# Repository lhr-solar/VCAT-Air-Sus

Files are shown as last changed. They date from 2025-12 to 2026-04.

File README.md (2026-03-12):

# Air-Suspension Boards

> **Project:** Longhorn Racing Solar - Hardware & Telemetry
> **Author:** Karthik Kurapati 

This repository contains the hardware design files for 4 sensors on the car: Suspension (Linear Potentiometers), Pitot, Temperature/Pressure, and RideHeight. 

## Table of Contents
1. [Telemetry CAN Overview](#CAN-overview)
2. [PSOM Boards](#psom-boards)
    - [Pitot Board](#1-pitot-board)
    - [Sus-RH (Suspension & Ride Height) Board](#2-sus-rh-board)
3. [Breakout Boards](#breakout-boards)
    - [Temperature Breakout](#3-temperature-breakout)
    - [Ride Height Breakout](#4-ride-height-breakout)

---

## Telemetry CAN Overview

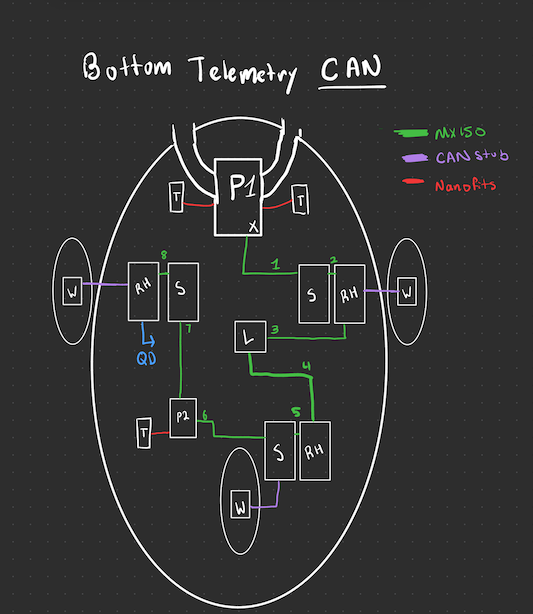
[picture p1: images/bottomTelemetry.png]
System Block Diagram


P - Pitot Board
T - Temperature Breakout
L - Telemetry Leader
S - Sus-RH Board
RH - Sus-RH Board + Ride Height Breakout
W - Wheels Board

---

## PSOM Boards

These boards integrate a PSOM to collect data from sensors 

### 1. Pitot Board
**Function:** Measures the vehicle's true airspeed via a pitot sensor. Relays data sent by the temperature sensor to telemetry leader. 
**Sensors**: HSCDRRN010NDSA3

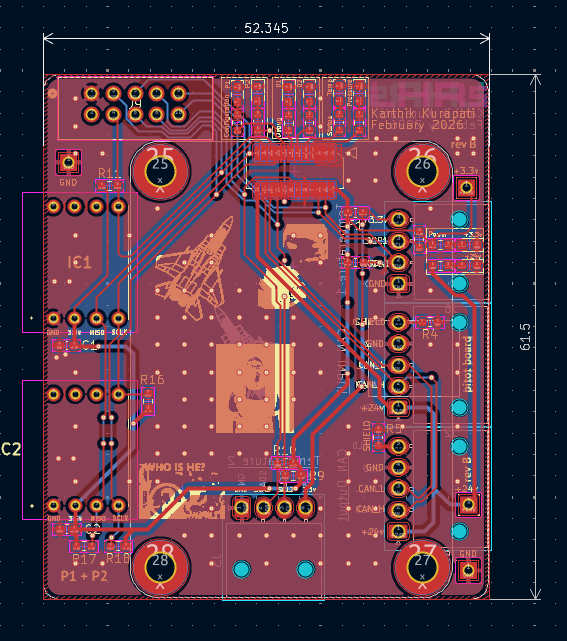
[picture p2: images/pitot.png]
Pitot Board


### 2. Sus-RH Board
**Function:** Measures linear potentiometer (suspension) travel on the car via ADC. Interfaces with ride height breakout. 
**Sensor:** LPPS-12
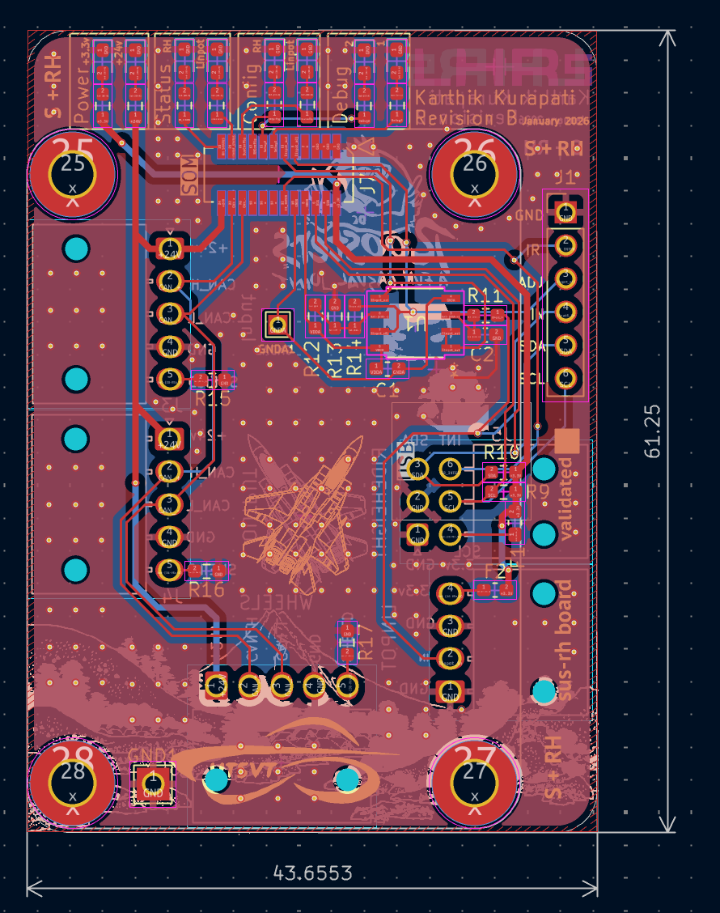
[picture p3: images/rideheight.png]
Sus-RH Board


---

## Breakout Boards

Simple boards that use nano-fits to connect to the boards above to add functionality. Both breakouts use I2C to communicate over the distance. 

### 3. Temperature Breakout
**Function:** Provide valuable temperature, pressure, humidity, and air density information to improve estimate of airspeed. 
**Sensor:** BME280 

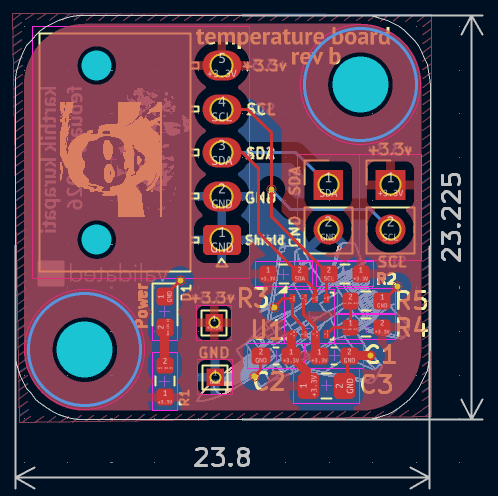
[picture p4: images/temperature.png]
Temp Breakout 3D Render/Photo


### 4. Ride Height Breakout (IR Board)
**Function:** Provides the distance from the bottom of the car to the road in multiple areas.
**Sensor** VL53L0X

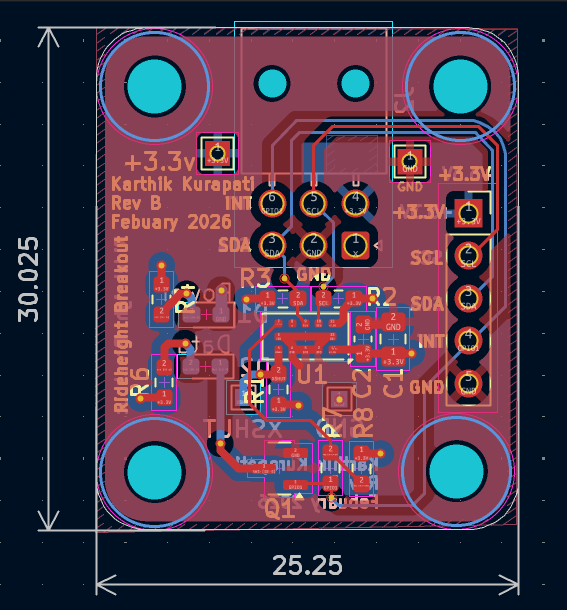
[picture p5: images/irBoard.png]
Ride Height Breakout 3D Render/Photo

---

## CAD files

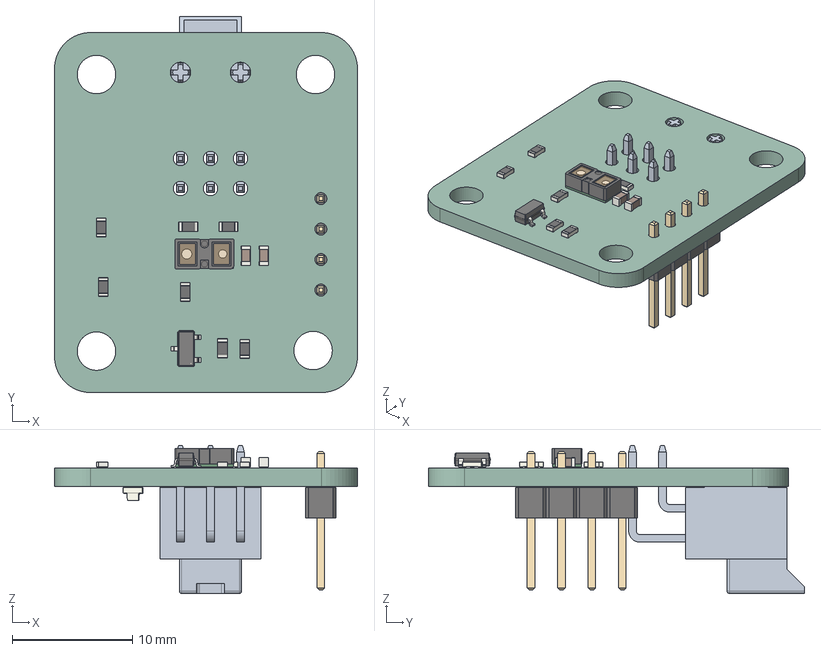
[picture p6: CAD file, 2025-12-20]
hardware/ir_board/ir_board.step
25.2 x 31.3 x 12.3 mm
ST_VL53L1x
R_0603_1608Metric x 7
C_0603_1608Metric x 2
SOT-23
LED_0603_1608Metric x 2
PinHeader_1x04_P2.54mm_Vertical
ir_board_PCB

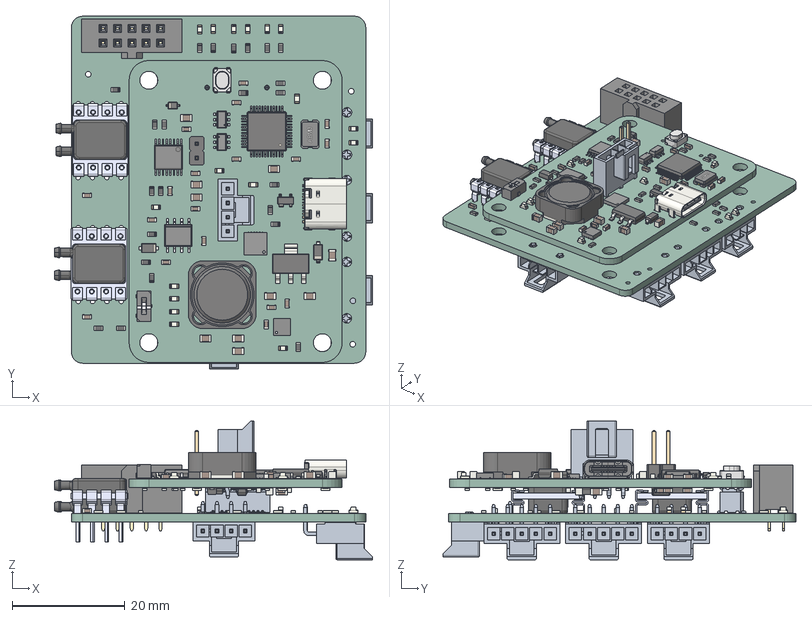
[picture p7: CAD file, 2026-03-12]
hardware/Pitot/Pitot.step
56.3 x 62.5 x 24.6 mm
R_0603_1608Metric x 49
C_0603_1608Metric x 27
D_SOD-123F x 2
LED_0603_1608Metric x 17
ThermalPin
PinsArrayLR x 3
PinsArrayTB
C_0805_2012Metric x 12
LQFP-48_7x7mm_P0.5mm
SOT-223
kicad_embedded_DC8F7DF302591227B9F71E251B6FE682
kicad_embedded_70E7614803E5E4F918B4D78DA69A18BB
L_Coilcraft_MSS1246-XXX
USB_C_Receptacle_GCT_USB4105-xx-A_16P_TopMnt_Horizontal
kicad_embedded_9406EA57197DC5EF7108E35EAA086FA7
BODY-SO x 2
LEAD-D0008A x 8
TL3365AF180QG--3DModel-STEP-520916
BODY-TSSOP
LEAD-TSSOP x 16
PIN1
DAP
SOT-143
D_SOD-123
PinHeader_1x02_P2.54mm_Vertical
D_SOD-323
SOT-23W
LEAD-SO x 8
PeripheralSOM_PCB
Fuse_0603_1608Metric
HSCDRRN010NDSA3 x 2
SFH11-xC-Dx-ST-BK body_05
pin^SFH11-xC-Dx-ST-BK Ass x 10
Pitot_PCB

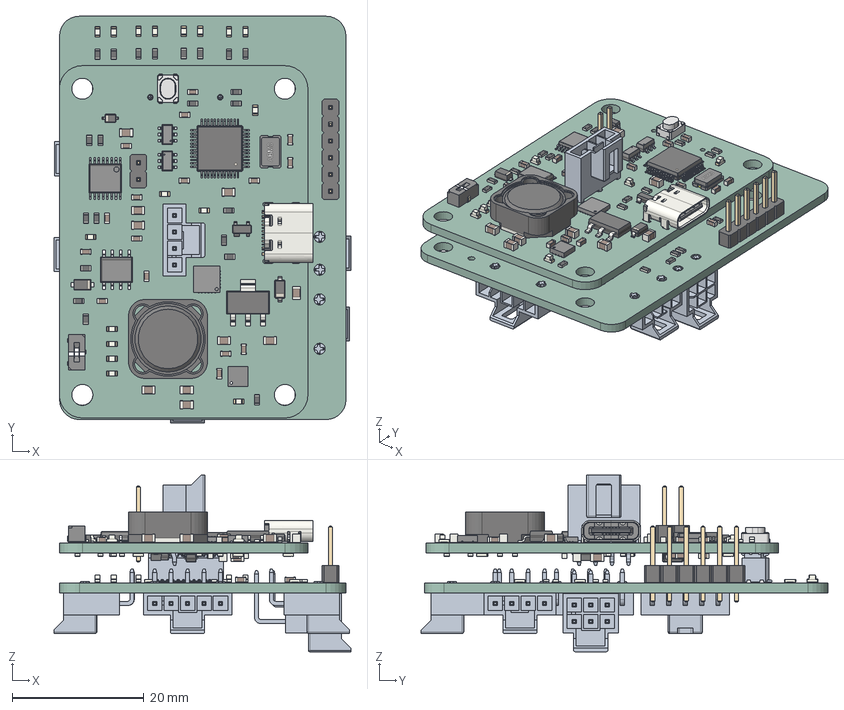
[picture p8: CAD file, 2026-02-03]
hardware/Sus-RH/Sus-RH.step
45.1 x 61.7 x 26.8 mm
LED_0603_1608Metric x 17
Fuse_0603_1608Metric x 2
R_0603_1608Metric x 48
C_0603_1608Metric x 27
D_SOD-123F x 2
ThermalPin
PinsArrayLR x 3
PinsArrayTB
C_0805_2012Metric x 12
LQFP-48_7x7mm_P0.5mm
SOT-223
kicad_embedded_DC8F7DF302591227B9F71E251B6FE682
kicad_embedded_70E7614803E5E4F918B4D78DA69A18BB
L_Coilcraft_MSS1246-XXX
USB_C_Receptacle_GCT_USB4105-xx-A_16P_TopMnt_Horizontal
kicad_embedded_9406EA57197DC5EF7108E35EAA086FA7
BODY-SO x 2
LEAD-D0008A x 8
TL3365AF180QG--3DModel-STEP-520916
BODY-TSSOP
LEAD-TSSOP x 16
PIN1
DAP
SOT-143
D_SOD-123
PinHeader_1x02_P2.54mm_Vertical
D_SOD-323
SOT-23W
LEAD-SO x 8
PeripheralSOM_PCB
PinHeader_1x06_P2.54mm_Vertical
Sus-RH_PCB

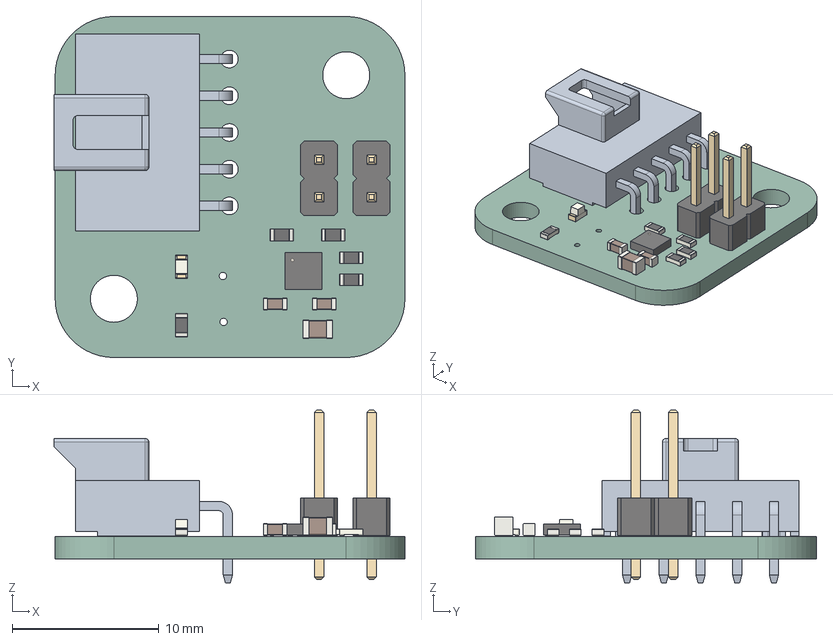
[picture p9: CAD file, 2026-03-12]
hardware/TempBoard/TempBoard.step
23.9 x 23.2 x 11.8 mm
R_0603_1608Metric x 5
C_0603_1608Metric x 2
Bosch_LGA-8_2.5x2.5mm_P0.65mm_ClockwisePinNumbering
C_0805_2012Metric
LED_0603_1608Metric
PinHeader_1x02_P2.54mm_Vertical x 2
TempBoard_PCB

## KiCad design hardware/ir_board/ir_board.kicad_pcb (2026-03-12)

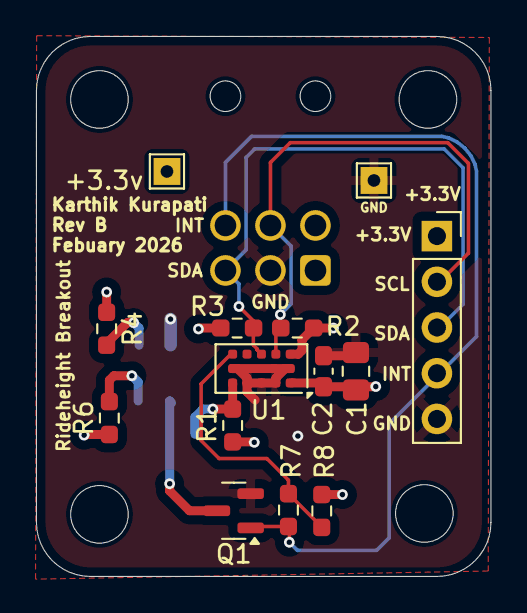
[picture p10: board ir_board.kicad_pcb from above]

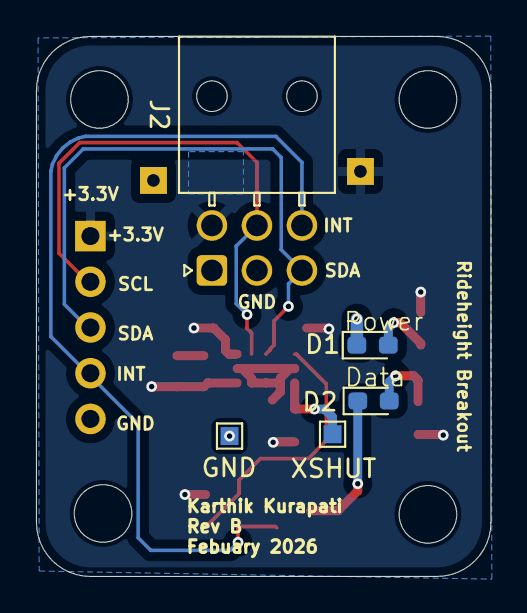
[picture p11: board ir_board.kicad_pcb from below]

Board: 2 copper layers, 25.2 x 30.0 mm, 23 parts (5 on the bottom side), 10 nets.

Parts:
+3.3v: TestPoint; TestPoint_THTPad_1.5x1.5mm_Drill0.7mm
C1: 4.7uf; C_0805_2012Metric_Pad1.18x1.45mm_HandSolder
C2: 0.1uf; C_0603_1608Metric_Pad1.08x0.95mm_HandSolder
D1, D2: LED; LED_0603_1608Metric_Pad1.05x0.95mm_HandSolder
GND: TestPoint; TestPoint_THTPad_1.5x1.5mm_Drill0.7mm
GND#2: TestPoint; TestPoint_Pad_1.0x1.0mm
H1, H2, H3, H4: MountingHole; MountingHole_3.2mm_M3
J1: Conn_01x05; PinSocket_1x05_P2.54mm_Vertical
J2: Conn_01x06; Molex_Nano-Fit_105314-xx06_2x03_P2.50mm_Horizontal
Q1: IRLML0030; SOT-23
R1: 10k; R_0603_1608Metric_Pad0.98x0.95mm_HandSolder
R2, R3, R8: 4.7k; R_0603_1608Metric_Pad0.98x0.95mm_HandSolder
R4, R6: 1k; R_0603_1608Metric_Pad0.98x0.95mm_HandSolder
R7: 0; R_0603_1608Metric_Pad0.98x0.95mm_HandSolder
U1: VL53L0CXV0DH1; ST_VL53L1x
XSHUT: TestPoint; TestPoint_Pad_1.0x1.0mm

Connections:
+3.3V: +3.3v.1, C1.1, C2.1, J1.1, J2.4, R1.1, R2.1, R3.1, R4.1, R6.1, R8.1, U1.1 (AVDDVCSEL), U1.11 (AVDD)
/GPIO1: J1.4, J2.6, Q1.1 (G), R7.1
/SCL: J1.2, J2.5, R2.2, U1.10 (SCL)
/SDA: J1.3, J2.3, R3.2, U1.9 (SDA)
/XSHUT: R1.2, U1.5 (XSHUT), XSHUT.1
GND: C1.2, C2.2, D1.1 (K), GND.1, GND#2.1, J1.5, J2.2, Q1.2 (S), U1.2 (AVSSVCSEL), U1.3 (GND), U1.4 (GND), U1.6 (GND), U1.12 (GND)
unnamed: D1.2 (A), R4.2
unnamed: D2.2 (A), R6.2
unnamed: D2.1 (K), Q1.3 (D)
unnamed: R7.2, R8.2, U1.7 (GPIO1)

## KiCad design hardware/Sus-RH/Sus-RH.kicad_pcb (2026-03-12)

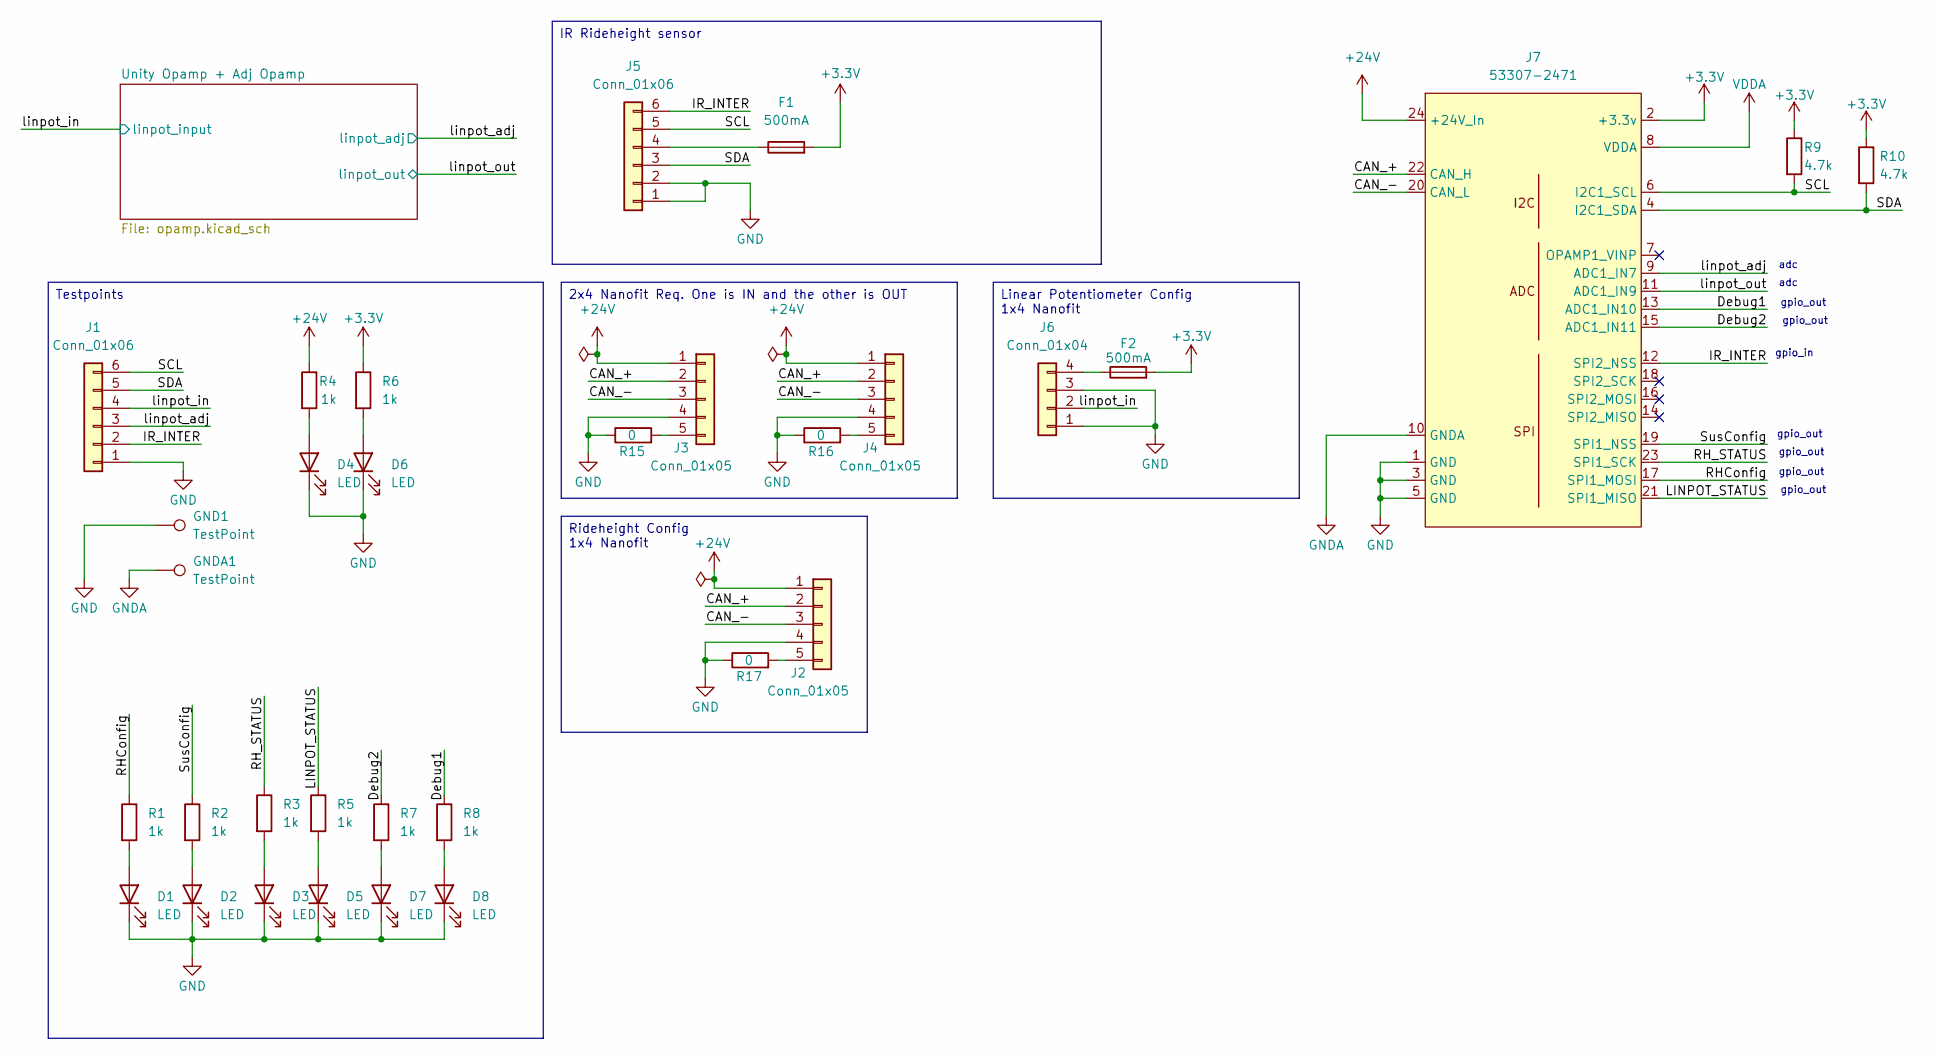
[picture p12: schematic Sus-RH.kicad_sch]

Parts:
D1, D2, D3, D4, D5, D6, D7, D8: LED; LED_0603_1608Metric_Pad1.05x0.95mm_HandSolder
F1, F2: 500mA; Fuse_0603_1608Metric_Pad1.05x0.95mm_HandSolder
GND1: TestPoint; TestPoint_THTPad_2.5x2.5mm_Drill1.2mm
GNDA1: TestPoint; TestPoint_THTPad_1.5x1.5mm_Drill0.7mm
J1: Conn_01x06; PinHeader_1x06_P2.54mm_Vertical
J2, J3, J4: Conn_01x05; Molex_Nano-Fit_105313-xx05_1x05_P2.50mm_Horizontal
J5: Conn_01x06; Molex_Nano-Fit_105314-xx06_2x03_P2.50mm_Horizontal
J6: Conn_01x04; Molex_Nano-Fit_105313-xx04_1x04_P2.50mm_Horizontal
J7: 53307-2471; PeripheralSOM
R1, R2, R3, R4, R5, R6, R7, R8: 1k; R_0603_1608Metric_Pad0.98x0.95mm_HandSolder
R9, R10: 4.7k; R_0603_1608Metric_Pad0.98x0.95mm_HandSolder
R15, R16, R17: 0; R_0603_1608Metric_Pad0.98x0.95mm_HandSolder

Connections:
+3.3V: F1.2, F2.2, J7.2 (+3.3v), R6.1, R9.1, R10.1
+24V: J2.1, J3.1, J4.1, J7.24 (+24V_In), R4.1
/CAN_+: J2.2, J3.2, J4.2, J7.22 (CAN_H)
/CAN_-: J2.3, J3.3, J4.3, J7.20 (CAN_L)
/Debug1: J7.13 (ADC1_IN10), R8.1
/Debug2: J7.15 (ADC1_IN11), R7.1
/IR_INTER: J1.2, J5.6, J7.12 (SPI2_NSS)
/LINPOT_STATUS: J7.21 (SPI1_MISO), R5.1
/RHConfig: J7.17 (SPI1_MOSI), R1.1
/RH_STATUS: J7.23 (SPI1_SCK), R3.1
/SCL: J1.6, J5.5, J7.6 (I2C1_SCL), R9.2
/SDA: J1.5, J5.3, J7.4 (I2C1_SDA), R10.2
/SusConfig: J7.19 (SPI1_NSS), R2.1
/linpot_adj: J1.3, J7.9 (ADC1_IN7); also elsewhere on the board
/linpot_in: J1.4, J6.2; also elsewhere on the board
/linpot_out: J7.11 (ADC1_IN9); also elsewhere on the board
GND: D1.1 (K), D2.1 (K), D3.1 (K), D4.1 (K), D5.1 (K), D6.1 (K), D7.1 (K), D8.1 (K), GND1.1, J1.1, J2.4, J3.4, J4.4, J5.1, J5.2, J6.1, J6.3, J7.1 (GND), J7.3 (GND), J7.5 (GND), R15.1, R16.1, R17.1; also elsewhere on the board
GNDA: GNDA1.1, J7.10 (GNDA); also elsewhere on the board
unnamed: D1.2 (A), R1.2
unnamed: D2.2 (A), R2.2
unnamed: D3.2 (A), R3.2
unnamed: D4.2 (A), R4.2
unnamed: D5.2 (A), R5.2
unnamed: D6.2 (A), R6.2
unnamed: D7.2 (A), R7.2
unnamed: D8.2 (A), R8.2
unnamed: J2.5, R17.2
unnamed: J3.5, R15.2
unnamed: J4.5, R16.2
unnamed: F1.1, J5.4
unnamed: F2.1, J6.4
VDDA: J7.8 (VDDA); also elsewhere on the board

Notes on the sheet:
gpio_in
adc
gpio_out
Rideheight Config 1x4 Nanofit
IR Rideheight sensor
2x4 Nanofit Req. One is IN and the other is OUT
Testpoints
Linear Potentiometer Config 1x4 Nanofit

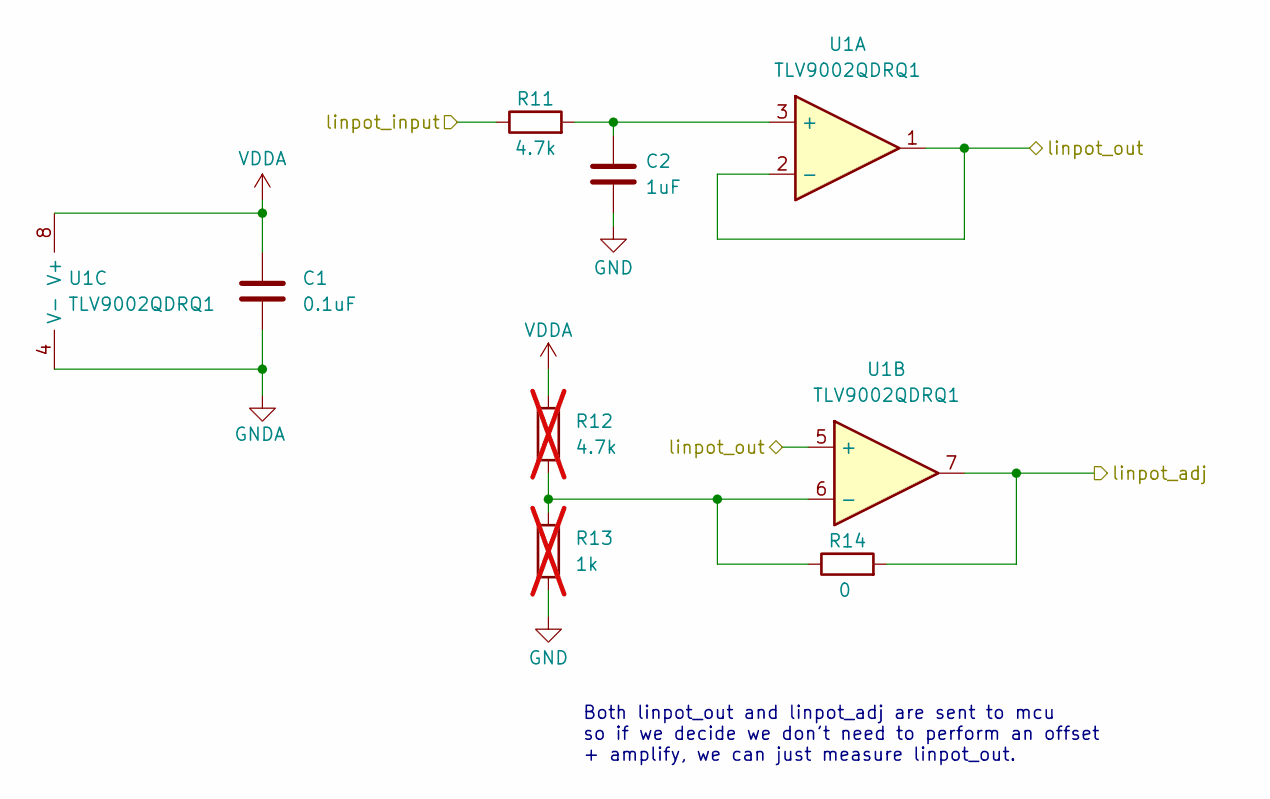
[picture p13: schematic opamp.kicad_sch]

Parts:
C1: 0.1uF; C_0603_1608Metric_Pad1.08x0.95mm_HandSolder
C2: 1uF; C_0603_1608Metric_Pad1.08x0.95mm_HandSolder
R11: 4.7k; R_0603_1608Metric_Pad0.98x0.95mm_HandSolder
R12: 4.7k; R_0603_1608Metric_Pad0.98x0.95mm_HandSolder; not fitted
R13: 1k; R_0603_1608Metric_Pad0.98x0.95mm_HandSolder; not fitted
R14: 0; R_0603_1608Metric_Pad0.98x0.95mm_HandSolder
U1: TLV9002QDRQ1; SOIC8_D_TEX; Mouser P/N 595-TLV9002QDRQ1

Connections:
/linpot_adj: R14.2, U1.7; also elsewhere on the board
/linpot_in: R11.1; also elsewhere on the board
/linpot_out: U1.1, U1.2 (-), U1.5 (+); also elsewhere on the board
GND: C2.2, R13.2; also elsewhere on the board
GNDA: C1.2, U1.4 (V-); also elsewhere on the board
unnamed: C2.1, R11.2, U1.3 (+)
unnamed: R12.2, R13.1, R14.1, U1.6 (-)
VDDA: C1.1, R12.1, U1.8 (V+); also elsewhere on the board

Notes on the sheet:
Both linpot_out and linpot_adj are sent to mcu so if we decide we don't need to perform an offset + amplify, we can just measure linpot_out.

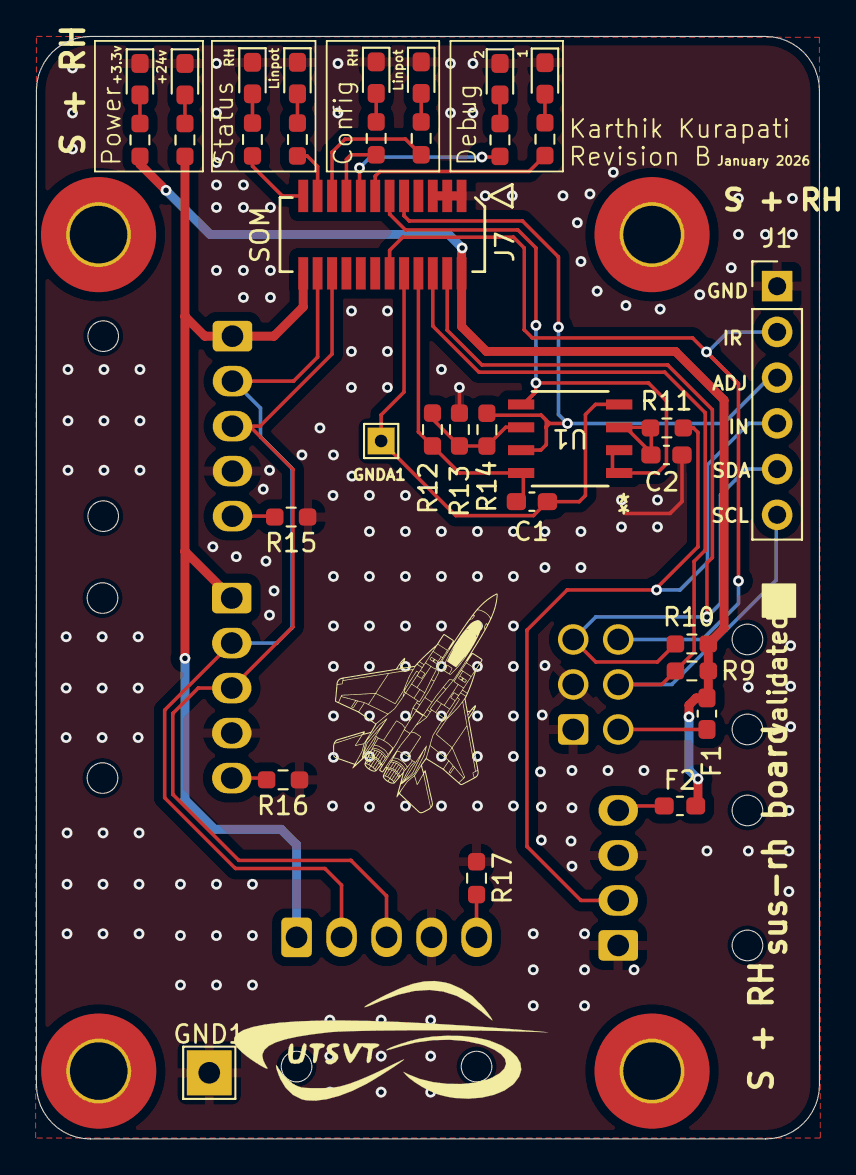
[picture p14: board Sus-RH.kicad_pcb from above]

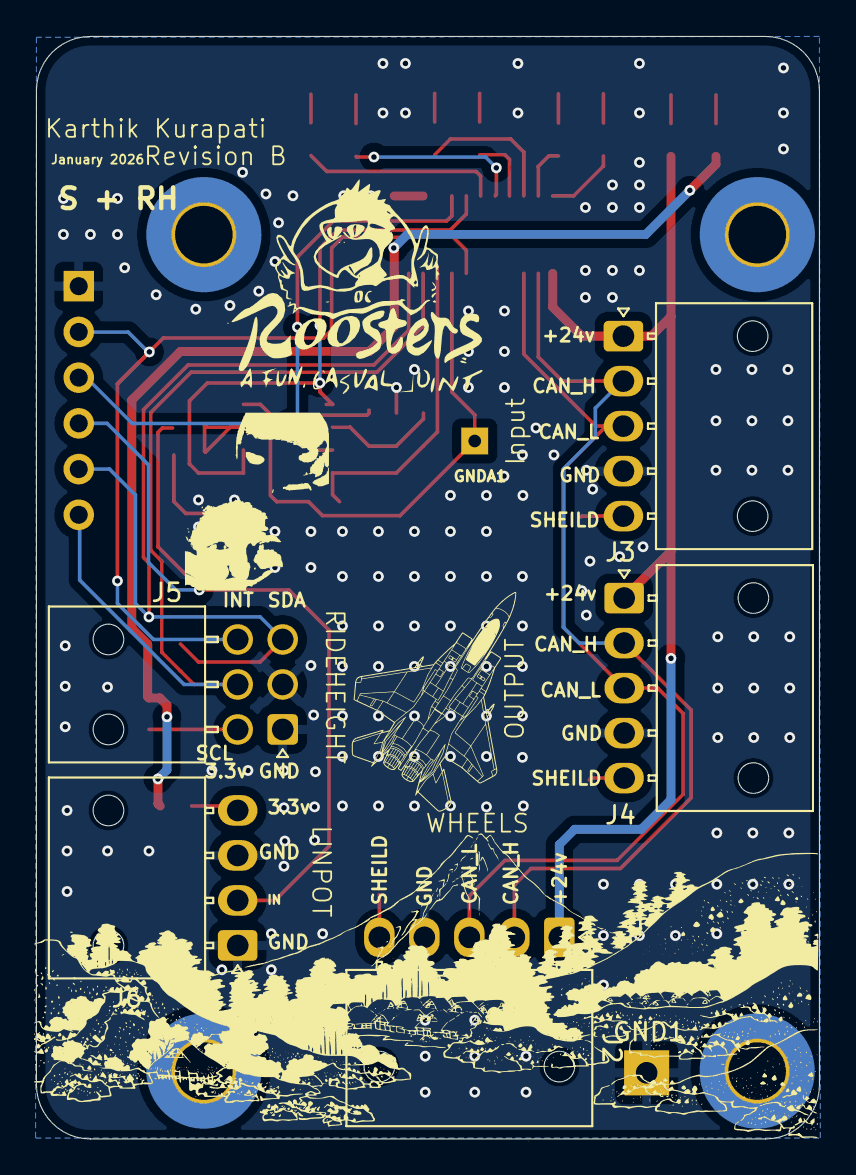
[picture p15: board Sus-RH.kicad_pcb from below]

Board: 2 copper layers, 43.5 x 61.2 mm, 39 parts (5 on the bottom side), 34 nets.

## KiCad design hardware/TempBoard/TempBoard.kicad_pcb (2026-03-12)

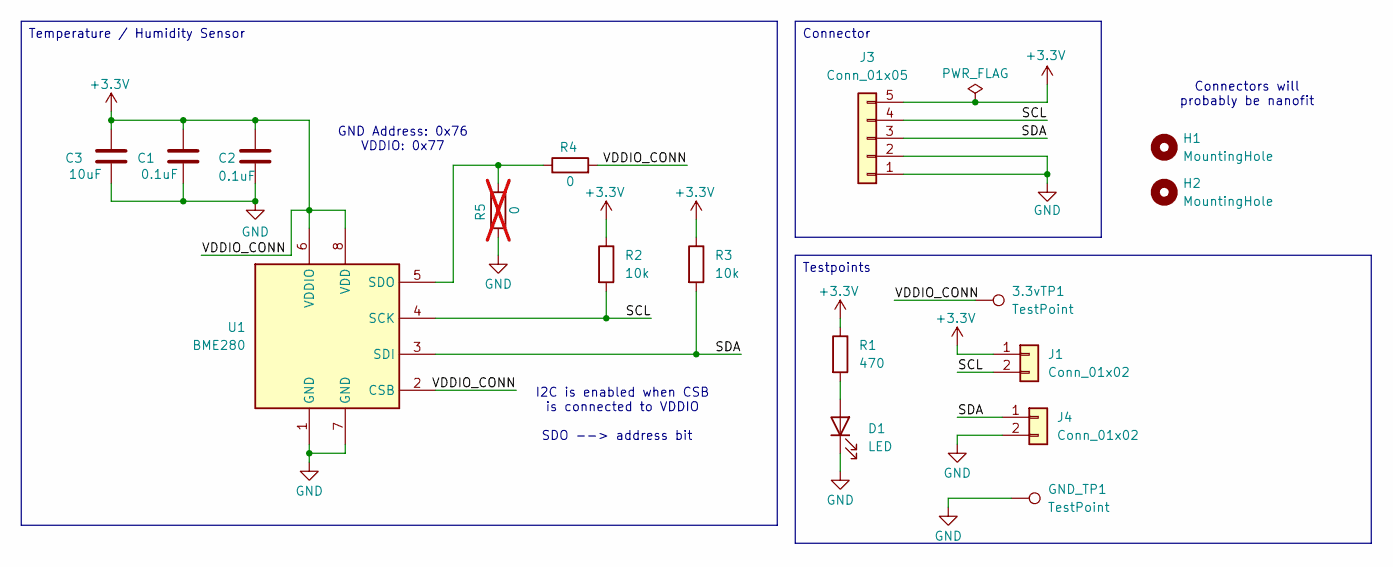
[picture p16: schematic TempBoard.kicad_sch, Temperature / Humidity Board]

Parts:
3.3vTP1: TestPoint; TestPoint_THTPad_1.0x1.0mm_Drill0.5mm
C1, C2: 0.1uF; C_0603_1608Metric_Pad1.08x0.95mm_HandSolder
C3: 10uF; C_0805_2012Metric_Pad1.18x1.45mm_HandSolder
D1: LED; LED_0603_1608Metric_Pad1.05x0.95mm_HandSolder
GND_TP1: TestPoint; TestPoint_THTPad_1.0x1.0mm_Drill0.5mm
H1, H2: MountingHole; MountingHole_3.2mm_M3
J1, J4: Conn_01x02; PinHeader_1x02_P2.54mm_Vertical
J3: Conn_01x05; Molex_Nano-Fit_105313-xx05_1x05_P2.50mm_Horizontal
R1: 470; R_0603_1608Metric_Pad0.98x0.95mm_HandSolder
R2, R3: 10k; R_0603_1608Metric_Pad0.98x0.95mm_HandSolder
R4: 0; R_0603_1608Metric_Pad0.98x0.95mm_HandSolder
R5: 0; R_0603_1608Metric_Pad0.98x0.95mm_HandSolder; not fitted
U1: BME280; Bosch_LGA-8_2.5x2.5mm_P0.65mm_ClockwisePinNumbering

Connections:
+3.3V: 3.3vTP1.1, C1.1, C2.1, C3.1, J1.1, J3.5, R1.1, R2.1, R3.1, R4.2, U1.2 (CSB), U1.6 (VDDIO), U1.8 (VDD)
/SCL: J1.2, J3.4, R2.2, U1.4 (SCK)
/SDA: J3.3, J4.1, R3.2, U1.3 (SDI)
GND: C1.2, C2.2, C3.2, D1.1 (K), GND_TP1.1, J3.1, J3.2, J4.2, R5.1, U1.1 (GND), U1.7 (GND)
unnamed: D1.2 (A), R1.2
unnamed: R4.1, R5.2, U1.5 (SDO)

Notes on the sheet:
Connectors will probably be nanofit
I2C is enabled when CSB is connected to VDDIO
GND Address: 0x76 VDDIO: 0x77
SDO --> address bit
Connector
Testpoints
Temperature / Humidity Sensor

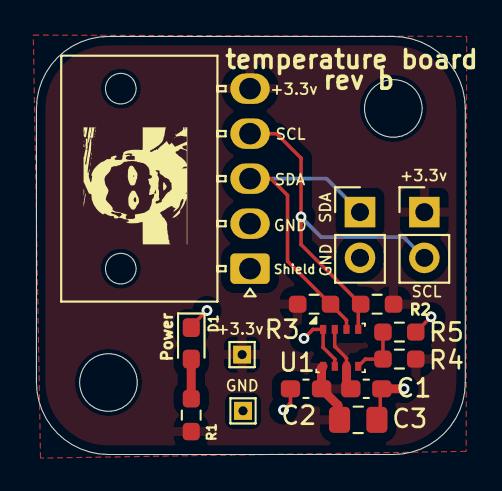
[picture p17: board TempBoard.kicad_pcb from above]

Board: 2 copper layers, 23.8 x 23.2 mm, 17 parts (0 on the bottom side), 6 nets.

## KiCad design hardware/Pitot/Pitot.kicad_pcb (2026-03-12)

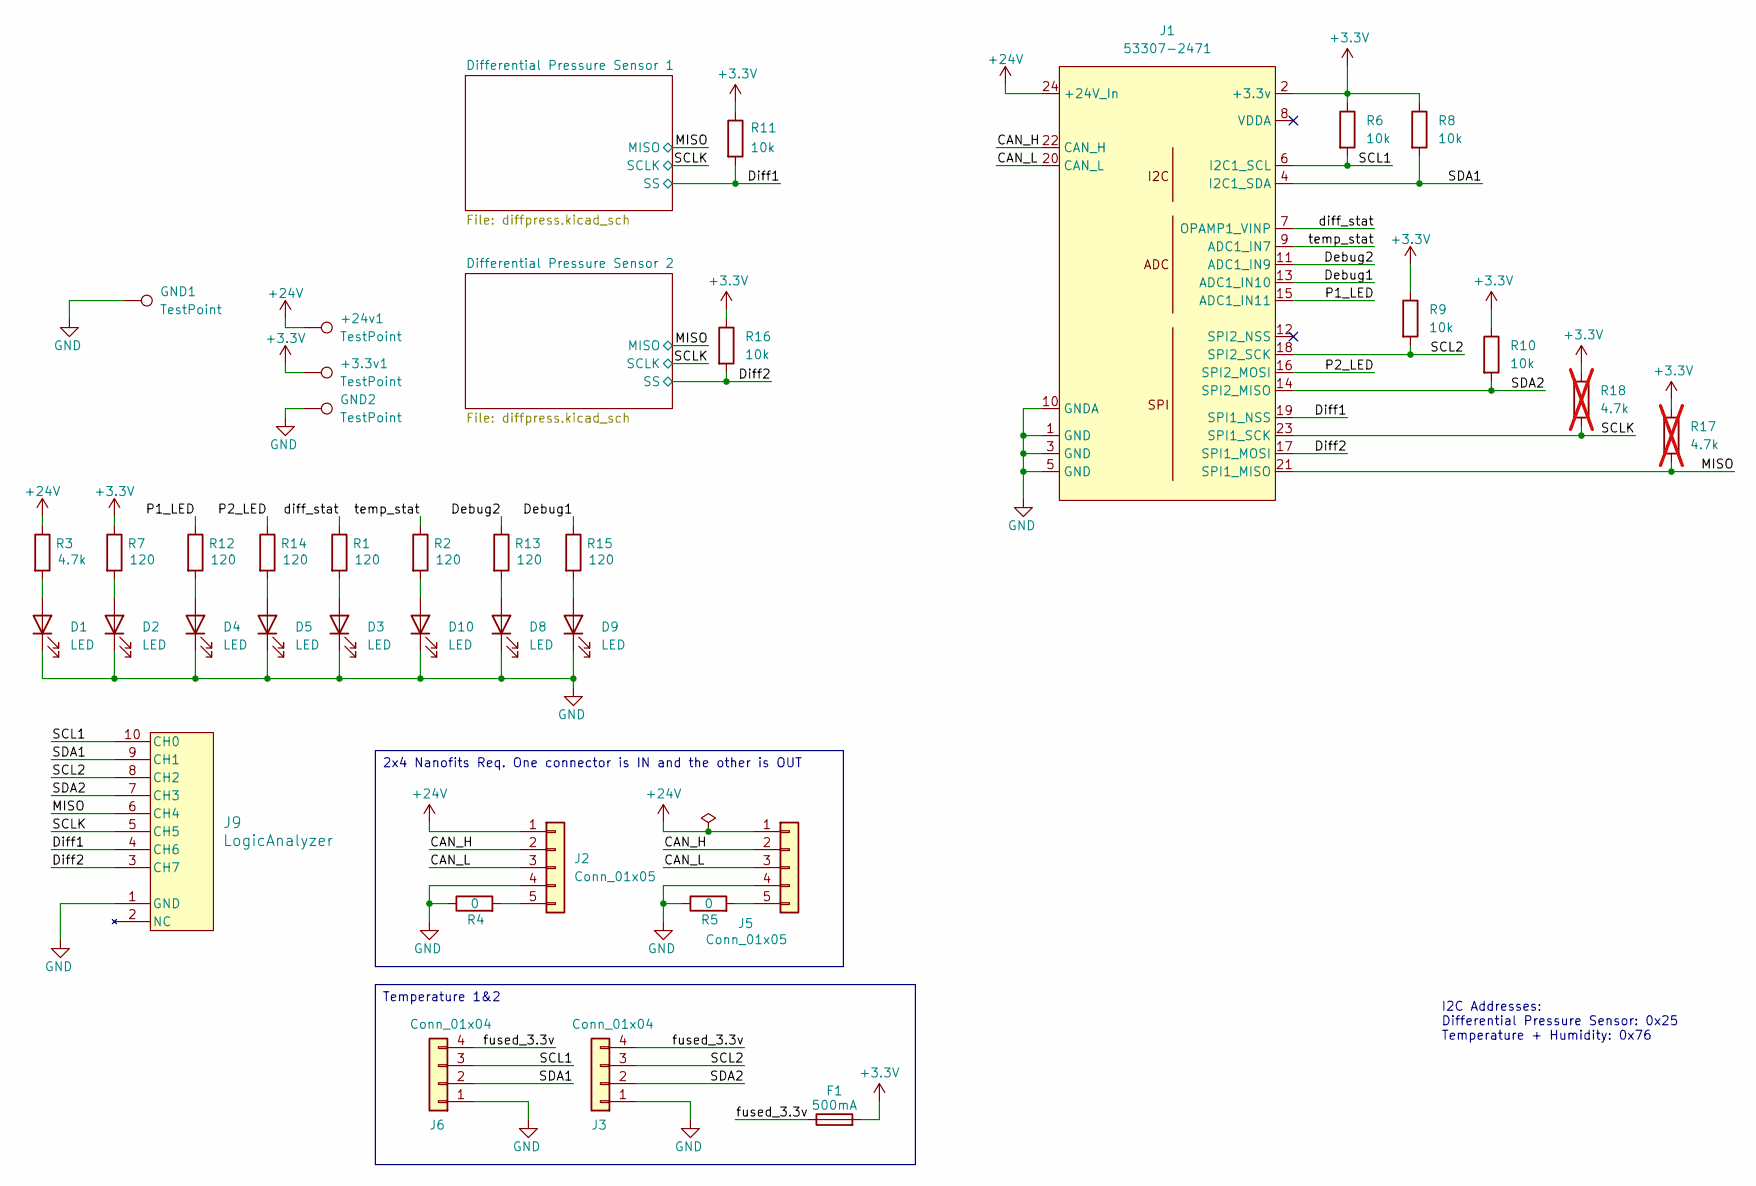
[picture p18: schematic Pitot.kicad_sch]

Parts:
+3.3v1, +24v1: TestPoint; TestPoint_THTPad_2.0x2.0mm_Drill1.0mm
D1, D5, D8, D10: LED; LED_0603_1608Metric_Pad1.05x0.95mm_HandSolder; JLC P/N C7371904
D2, D3, D4, D9: LED; LED_0603_1608Metric_Pad1.05x0.95mm_HandSolder; JLC P/N C84263
F1: 500mA; Fuse_0603_1608Metric_Pad1.05x0.95mm_HandSolder
GND1, GND2: TestPoint; TestPoint_THTPad_2.0x2.0mm_Drill1.0mm
J1: 53307-2471; PeripheralSOM
J2, J5: Conn_01x05; Molex_Nano-Fit_105313-xx05_1x05_P2.50mm_Horizontal
J3, J6: Conn_01x04; Molex_Nano-Fit_105313-xx04_1x04_P2.50mm_Horizontal
J9: LogicAnalyzer; CONN_SFH11-xxxC-D05-ST-XX_SUL; Digikey P/N S9194-ND
R1, R2, R7, R12, R13, R14, R15: 120; R_0603_1608Metric_Pad0.98x0.95mm_HandSolder
R3: 4.7k; R_0603_1608Metric_Pad0.98x0.95mm_HandSolder
R4, R5: 0; R_0603_1608Metric_Pad0.98x0.95mm_HandSolder
R6, R8, R9, R10, R11, R16: 10k; R_0603_1608Metric_Pad0.98x0.95mm_HandSolder
R17, R18: 4.7k; R_0603_1608Metric_Pad0.98x0.95mm_HandSolder; not fitted

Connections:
+3.3V: +3.3v1.1, F1.2, J1.2 (+3.3v), R6.1, R7.1, R8.1, R9.1, R10.1, R11.1, R16.1, R17.1, R18.1; also elsewhere on the board
+24V: +24v1.1, J1.24 (+24V_In), J2.1, J5.1, R3.1
/CAN_H: J1.22 (CAN_H), J2.2, J5.2
/CAN_L: J1.20 (CAN_L), J2.3, J5.3
/Debug1: J1.13 (ADC1_IN10), R15.1
/Debug2: J1.11 (ADC1_IN9), R13.1
/Diff1: J1.19 (SPI1_NSS), J9.4 (CH6), R11.2; also elsewhere on the board
/Diff2: J1.17 (SPI1_MOSI), J9.3 (CH7), R16.2; also elsewhere on the board
/MISO: J1.21 (SPI1_MISO), J9.6 (CH4), R17.2; also elsewhere on the board
/P1_LED: J1.15 (ADC1_IN11), R12.1
/P2_LED: J1.16 (SPI2_MOSI), R14.1
/SCL1: J1.6 (I2C1_SCL), J6.3, J9.10 (CH0), R6.2
/SCL2: J1.18 (SPI2_SCK), J3.3, J9.8 (CH2), R9.2
/SCLK: J1.23 (SPI1_SCK), J9.5 (CH5), R18.2; also elsewhere on the board
/SDA1: J1.4 (I2C1_SDA), J6.2, J9.9 (CH1), R8.2
/SDA2: J1.14 (SPI2_MISO), J3.2, J9.7 (CH3), R10.2
/diff_stat: J1.7 (OPAMP1_VINP), R1.1
/fused_3.3v: F1.1, J3.4, J6.4
/temp_stat: J1.9 (ADC1_IN7), R2.1
GND: D1.1 (K), D2.1 (K), D3.1 (K), D4.1 (K), D5.1 (K), D8.1 (K), D9.1 (K), D10.1 (K), GND1.1, GND2.1, J1.1 (GND), J1.3 (GND), J1.5 (GND), J1.10 (GNDA), J2.4, J3.1, J5.4, J6.1, J9.1 (GND), R4.1, R5.1; also elsewhere on the board
unnamed: D1.2 (A), R3.2
unnamed: D2.2 (A), R7.2
unnamed: D3.2 (A), R1.2
unnamed: D4.2 (A), R12.2
unnamed: D5.2 (A), R14.2
unnamed: D8.2 (A), R13.2
unnamed: D9.2 (A), R15.2
unnamed: D10.2 (A), R2.2
unnamed: J2.5, R4.2
unnamed: J5.5, R5.2

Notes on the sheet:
I2C Addresses: Differential Pressure Sensor: 0x25 Temperature + Humidity: 0x76
Temperature 1&2
2x4 Nanofits Req. One connector is IN and the other is OUT

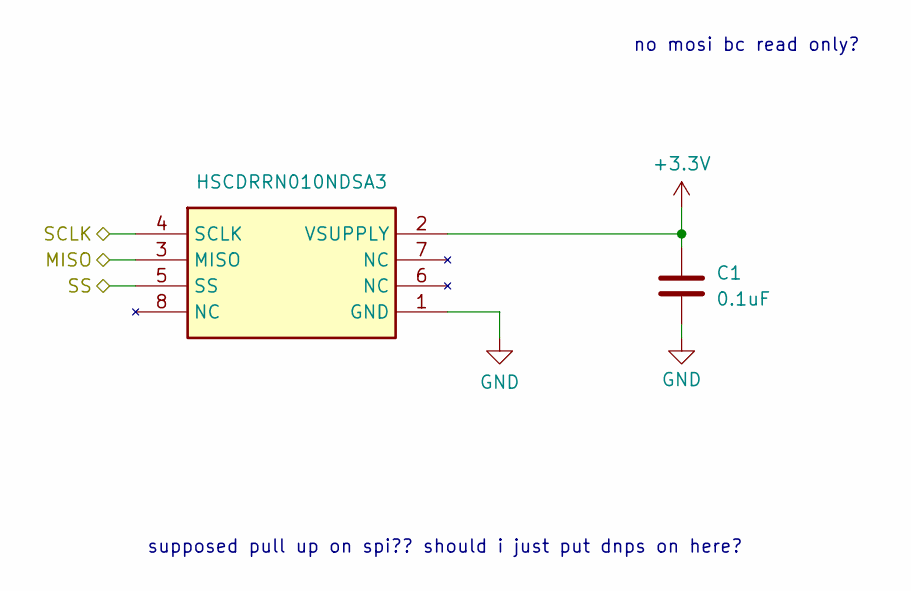
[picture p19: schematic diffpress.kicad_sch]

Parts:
C1: 0.1uF; C_0603_1608Metric_Pad1.08x0.95mm_HandSolder
IC1: HSCDRRN010NDSA3

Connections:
+3.3V: C1.1, IC1.2 (VSUPPLY); also elsewhere on the board
/Diff1: IC1.5 (SS); also elsewhere on the board
/MISO: IC1.3 (MISO); also elsewhere on the board
/SCLK: IC1.4 (SCLK); also elsewhere on the board
GND: C1.2, IC1.1 (GND); also elsewhere on the board

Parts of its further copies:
C2: 0.1uF; C_0603_1608Metric_Pad1.08x0.95mm_HandSolder
IC2: HSCDRRN010NDSA3

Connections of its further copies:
+3.3V: C2.1, IC2.2 (VSUPPLY); also elsewhere on the board
/Diff2: IC2.5 (SS); also elsewhere on the board
/MISO: IC2.3 (MISO); also elsewhere on the board
/SCLK: IC2.4 (SCLK); also elsewhere on the board
GND: C2.2, IC2.1 (GND); also elsewhere on the board

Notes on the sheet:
supposed pull up on spi?? should i just put dnps on here?
no mosi bc read only?

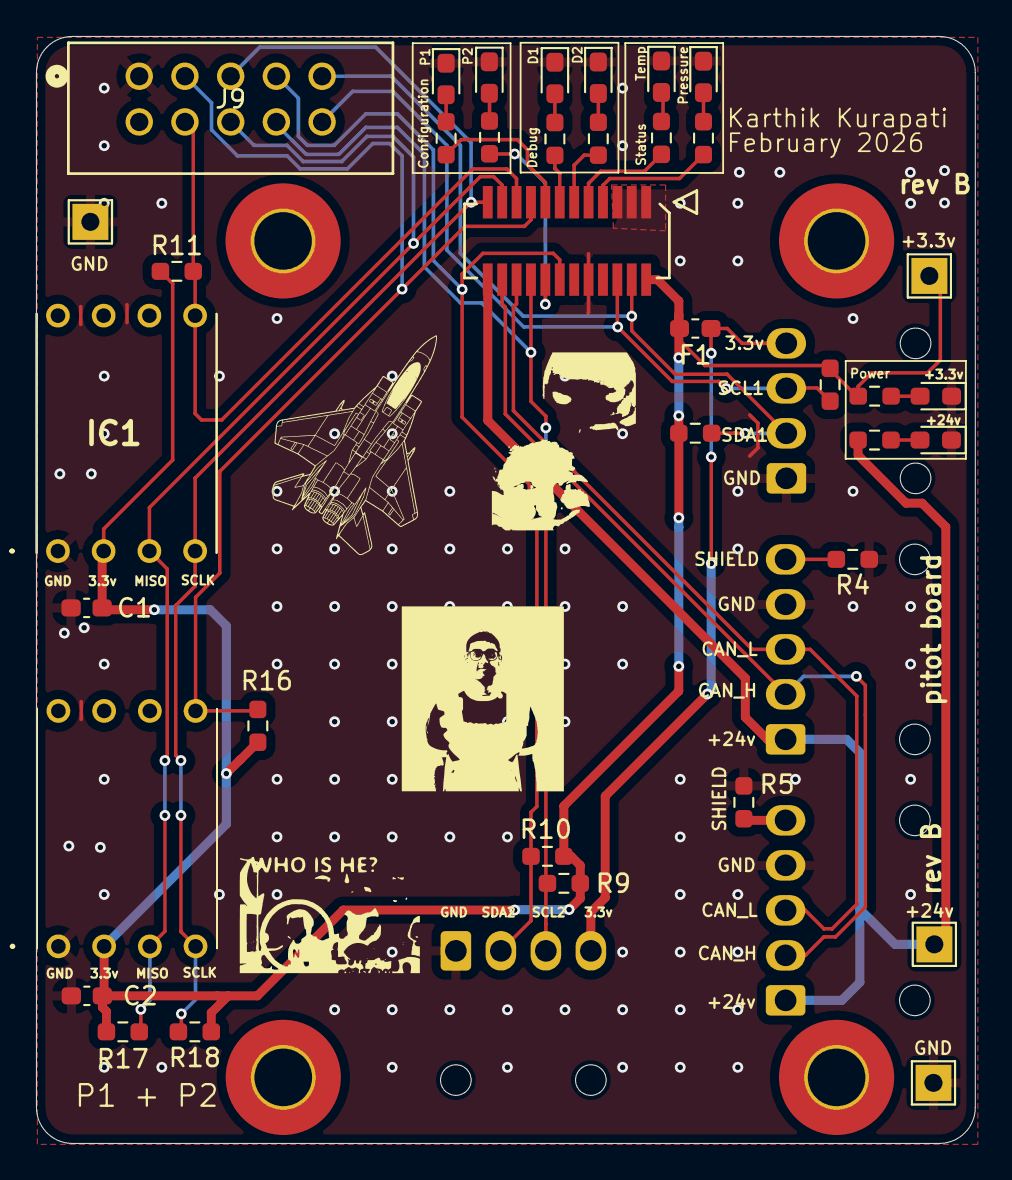
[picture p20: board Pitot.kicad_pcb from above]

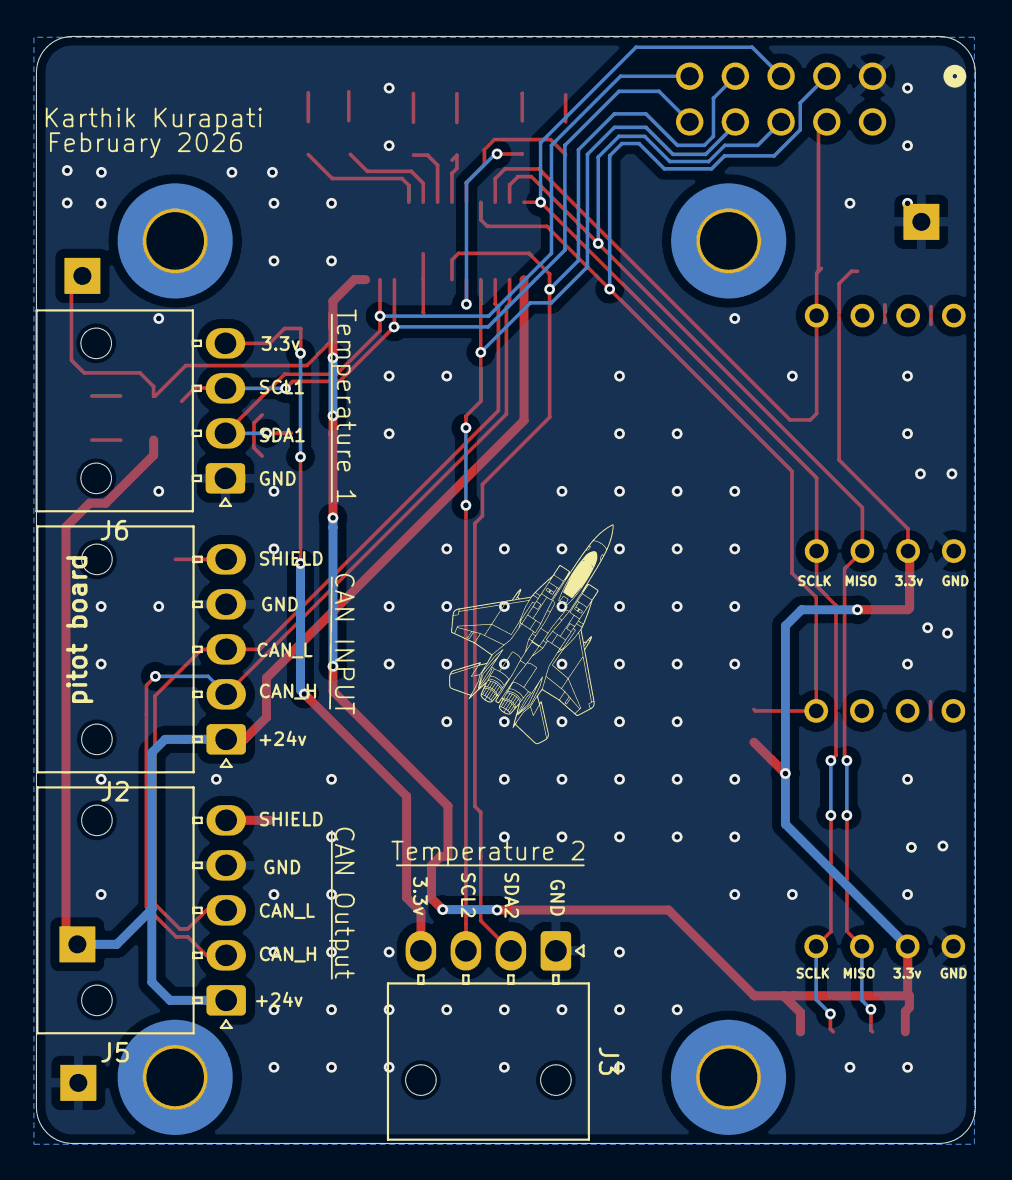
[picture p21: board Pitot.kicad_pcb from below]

Board: 2 copper layers, 52.2 x 61.5 mm, 41 parts (4 on the bottom side), 30 nets.

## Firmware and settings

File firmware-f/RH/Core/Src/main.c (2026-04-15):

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
/* Includes ------------------------------------------------------------------*/
#include "main.h"

/* USER CODE BEGIN Includes */
#include <stdio.h>
#include <string.h>
#include "vl53l0x_api.h"
#include "can_fifo.h"
/* USER CODE END Includes */

ADC_HandleTypeDef hadc1;

CAN_HandleTypeDef hcan1;

I2C_HandleTypeDef hi2c1;

TIM_HandleTypeDef htim2;

UART_HandleTypeDef huart1;

/* USER CODE BEGIN PV */
volatile uint8_t timer_10hz_flag = 0;

CircularFIFO my_fifo;

PackedCANMSG msg_buffer[64];
/* USER CODE END PV */

void SystemClock_Config(void);
static void MX_GPIO_Init(void);
static void MX_ADC1_Init(void);
static void MX_USART1_UART_Init(void);
static void MX_I2C1_Init(void);
static void MX_CAN1_Init(void);
static void MX_TIM2_Init(void);
/**
  * @brief  The application entry point.
  * @retval int
  */
int main(void)
{

  /* MCU Configuration--------------------------------------------------------*/

  /* Reset of all peripherals, Initializes the Flash interface and the Systick. */
  HAL_Init();

  /* Configure the system clock */
  SystemClock_Config();

  /* Initialize all configured peripherals */
  MX_GPIO_Init();
  MX_ADC1_Init();
  MX_USART1_UART_Init();
  MX_I2C1_Init();
  MX_CAN1_Init();
  MX_TIM2_Init();
  /* USER CODE BEGIN 2 */
  HAL_Delay(100);

  CAN_TxHeaderTypeDef txHeader;
  txHeader.StdId = 0x404;
  txHeader.IDE = CAN_ID_STD;
  txHeader.RTR = CAN_RTR_DATA; // Data frame (not remote)
  txHeader.DLC = 2; // 8 data bytes
  txHeader.TransmitGlobalTime = DISABLE; // TTCM disabled → must be DISABLE

  uint32_t txMailbox;
  PackedCANMSG pack; 
  uint8_t dequeued = 0;

  VL53L0X_Dev_t MyDevice;
  VL53L0X_DEV Dev = &MyDevice;
  Dev->I2cDevAddr = 0x52;

  char msg[64];
  int len;

  len = sprintf(msg, "Initializing Sensor...\r\n");
  HAL_UART_Transmit(&huart1, (uint8_t*)msg, len, 100);

  VL53L0X_DataInit(Dev);
  VL53L0X_StaticInit(Dev);

  uint32_t refSpadCount;
  uint8_t isApertureSpads;
  uint8_t VhvSettings;
  uint8_t PhaseCal;

  VL53L0X_PerformRefSpadManagement(Dev, &refSpadCount, &isApertureSpads);
  VL53L0X_PerformRefCalibration(Dev, &VhvSettings, &PhaseCal);

  VL53L0X_SetMeasurementTimingBudgetMicroSeconds(Dev, 33000);
  VL53L0X_SetDeviceMode(Dev, VL53L0X_DEVICEMODE_CONTINUOUS_RANGING);
  VL53L0X_StartMeasurement(Dev);

  len = sprintf(msg, "VL53L0X Init Complete! Running at 10Hz.\r\n");
  HAL_UART_Transmit(&huart1, (uint8_t*)msg, len, 100);

  // Start the 10Hz timer

  fifo_init(&my_fifo, msg_buffer, 64);

  HAL_TIM_Base_Start_IT(&htim2);
  HAL_CAN_Start(&hcan1);

  CAN_FilterTypeDef filterConfig;
  filterConfig.FilterBank = 0;
  filterConfig.FilterMode = CAN_FILTERMODE_IDMASK;
  filterConfig.FilterScale = CAN_FILTERSCALE_32BIT;
  filterConfig.FilterIdHigh = 0x0000;
  filterConfig.FilterIdLow = 0x0000;
  filterConfig.FilterMaskIdHigh = 0x0000;
  filterConfig.FilterMaskIdLow = 0x0000;
  filterConfig.FilterFIFOAssignment = CAN_RX_FIFO0;
  filterConfig.FilterActivation = ENABLE;
  filterConfig.SlaveStartFilterBank = 14;

  HAL_CAN_ConfigFilter(&hcan1, &filterConfig);

  HAL_CAN_ActivateNotification(&hcan1, CAN_IT_RX_FIFO0_MSG_PENDING);

  HAL_NVIC_SetPriority(CAN1_RX0_IRQn, 0, 0);
  HAL_NVIC_EnableIRQ(CAN1_RX0_IRQn);


  /* USER CODE END 2 */

  /* Infinite loop */
  /* USER CODE BEGIN WHILE */
  while (1){
    if (timer_10hz_flag){
      timer_10hz_flag = 0;

      HAL_GPIO_TogglePin(GPIOB, GPIO_PIN_11);
      HAL_GPIO_TogglePin(GPIOA, GPIO_PIN_5);

      VL53L0X_RangingMeasurementData_t RangingData = {0};
      uint8_t dataReady = 0;
      uint32_t timeout_counter = 0;

      // Poll over I2C 
      while (dataReady == 0 && timeout_counter < 60){
        VL53L0X_GetMeasurementDataReady(Dev, &dataReady);
        HAL_Delay(1);
        timeout_counter++;
      }
      if(dataReady){
        VL53L0X_GetRangingMeasurementData(Dev, &RangingData);
        
        pack.canData[0] = (RangingData.RangeMilliMeter >> 8) & 0xFF;
        pack.canData[1] = (RangingData.RangeMilliMeter) & 0xFF;
        fifo_enqueue(&my_fifo,pack);
      }
      VL53L0X_ClearInterruptMask(Dev, 0);
    }

     if(HAL_CAN_GetTxMailboxesFreeLevel(&hcan1) > 0){
      __disable_irq(); // Start Pause/section that would be cooked
      dequeued = 0;
      if(fifo_is_empty(&my_fifo) == 0){
        fifo_dequeue(&my_fifo, &pack); 
        dequeued = 1;
      }
      __enable_irq(); // End section that would be cooked by race condition

      // Now this one can take however much time it needs to send out the data
      if(dequeued == 1){
        HAL_CAN_AddTxMessage(&hcan1, &txHeader, pack.canData , &txMailbox);
      }
    }

    // we want to turn on Error LED when buffer HAS data, but CAN isn't transmitting
    if(fifo_is_empty(&my_fifo) != 1 && HAL_CAN_GetTxMailboxesFreeLevel(&hcan1) == 0){
      // if you are here, the fifo is filling up, but CAN is stuck 
      HAL_GPIO_WritePin(GPIOA, GPIO_PIN_12, GPIO_PIN_SET);
    }else{
      HAL_GPIO_WritePin(GPIOA, GPIO_PIN_12, GPIO_PIN_RESET);
    }
  }
}

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
/* USER CODE BEGIN 4 */
/**
  * @brief  Timer period elapsed callback — fires at 10 Hz from TIM2.
  */
void HAL_TIM_PeriodElapsedCallback(TIM_HandleTypeDef *htim)
{
  if (htim->Instance == TIM2)
  {
    timer_10hz_flag = 1;
  }
}
/* USER CODE END 4 */
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


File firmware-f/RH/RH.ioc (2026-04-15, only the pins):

Mcu.UserName=STM32L431CBTx
PA10.Signal=USART1_RX
PA11.Signal=GPIO_Output
PA12.Signal=GPIO_Output
PA2.Signal=ADCx_IN7
PA4.Signal=ADCx_IN9
PA5.Signal=GPIO_Output
PA6.Signal=GPIO_Output
PA9.Signal=USART1_TX
PB11.Signal=GPIO_Output
PB6.Signal=I2C1_SCL
PB7.Signal=I2C1_SDA
PB8.Signal=CAN1_RX
PB9.Signal=CAN1_TX

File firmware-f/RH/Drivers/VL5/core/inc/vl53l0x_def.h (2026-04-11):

/*******************************************************************************
 * Copyright � 2016, STMicroelectronics International N.V.
All rights reserved.

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
THIS SOFTWARE IS PROVIDED BY THE COPYRIGHT HOLDERS AND CONTRIBUTORS "AS IS" AND
ANY EXPRESS OR IMPLIED WARRANTIES, INCLUDING, BUT NOT LIMITED TO, THE IMPLIED
WARRANTIES OF MERCHANTABILITY, FITNESS FOR A PARTICULAR PURPOSE, AND
NON-INFRINGEMENT OF INTELLECTUAL PROPERTY RIGHTS ARE DISCLAIMED.
IN NO EVENT SHALL STMICROELECTRONICS INTERNATIONAL N.V. BE LIABLE FOR ANY
DIRECT, INDIRECT, INCIDENTAL, SPECIAL, EXEMPLARY, OR CONSEQUENTIAL DAMAGES
(INCLUDING, BUT NOT LIMITED TO, PROCUREMENT OF SUBSTITUTE GOODS OR SERVICES;
LOSS OF USE, DATA, OR PROFITS; OR BUSINESS INTERRUPTION) HOWEVER CAUSED AND
ON ANY THEORY OF LIABILITY, WHETHER IN CONTRACT, STRICT LIABILITY, OR TORT
(INCLUDING NEGLIGENCE OR OTHERWISE) ARISING IN ANY WAY OUT OF THE USE OF THIS
SOFTWARE, EVEN IF ADVISED OF THE POSSIBILITY OF SUCH DAMAGE.
*******************************************************************************/

/**
 * @file VL53L0X_def.h
 *
 * @brief Type definitions for VL53L0X API.
 *
 */


#ifndef _VL53L0X_DEF_H_
#define _VL53L0X_DEF_H_


#ifdef __cplusplus
extern "C" {
#endif

/** @defgroup VL53L0X_globaldefine_group VL53L0X Defines
 *	@brief	  VL53L0X Defines
 *	@{
 */


/** PAL SPECIFICATION major version */
#define VL53L0X10_SPECIFICATION_VER_MAJOR   1
/** PAL SPECIFICATION minor version */
#define VL53L0X10_SPECIFICATION_VER_MINOR   2
/** PAL SPECIFICATION sub version */
#define VL53L0X10_SPECIFICATION_VER_SUB	   7
/** PAL SPECIFICATION sub version */
#define VL53L0X10_SPECIFICATION_VER_REVISION 1440

/** VL53L0X PAL IMPLEMENTATION major version */
#define VL53L0X10_IMPLEMENTATION_VER_MAJOR	1
/** VL53L0X PAL IMPLEMENTATION minor version */
#define VL53L0X10_IMPLEMENTATION_VER_MINOR	0
/** VL53L0X PAL IMPLEMENTATION sub version */
#define VL53L0X10_IMPLEMENTATION_VER_SUB		9
/** VL53L0X PAL IMPLEMENTATION sub version */
#define VL53L0X10_IMPLEMENTATION_VER_REVISION	3673

/** PAL SPECIFICATION major version */
#define VL53L0X_SPECIFICATION_VER_MAJOR	 1
/** PAL SPECIFICATION minor version */
#define VL53L0X_SPECIFICATION_VER_MINOR	 2
/** PAL SPECIFICATION sub version */
#define VL53L0X_SPECIFICATION_VER_SUB	 7
/** PAL SPECIFICATION sub version */
#define VL53L0X_SPECIFICATION_VER_REVISION 1440

/** VL53L0X PAL IMPLEMENTATION major version */
#define VL53L0X_IMPLEMENTATION_VER_MAJOR	  1
/** VL53L0X PAL IMPLEMENTATION minor version */
#define VL53L0X_IMPLEMENTATION_VER_MINOR	  0
/** VL53L0X PAL IMPLEMENTATION sub version */
#define VL53L0X_IMPLEMENTATION_VER_SUB	  4
/** VL53L0X PAL IMPLEMENTATION sub version */
#define VL53L0X_IMPLEMENTATION_VER_REVISION	  4960
#define VL53L0X_DEFAULT_MAX_LOOP 2000
#define VL53L0X_MAX_STRING_LENGTH 32


#include "../../../VL5/core/inc/vl53l0x_device.h"
#include "../../../VL5/platform/inc/vl53l0x_types.h"


/****************************************
 * PRIVATE define do not edit
 ****************************************/

/** @brief Defines the parameters of the Get Version Functions
 */
typedef struct {
	uint32_t	 revision; /*!< revision number */
	uint8_t		 major;	   /*!< major number */
	uint8_t		 minor;	   /*!< minor number */
	uint8_t		 build;	   /*!< build number */
} VL53L0X_Version_t;


/** @brief Defines the parameters of the Get Device Info Functions
 */
typedef struct {
	char Name[VL53L0X_MAX_STRING_LENGTH];
		/*!< Name of the Device e.g. Left_Distance */
	char Type[VL53L0X_MAX_STRING_LENGTH];
		/*!< Type of the Device e.g VL53L0X */
	char ProductId[VL53L0X_MAX_STRING_LENGTH];
		/*!< Product Identifier String	*/
	uint8_t ProductType;
		/*!< Product Type, VL53L0X = 1, VL53L1 = 2 */
	uint8_t ProductRevisionMajor;
		/*!< Product revision major */
	uint8_t ProductRevisionMinor;
		/*!< Product revision minor */
} VL53L0X_DeviceInfo_t;


/** @defgroup VL53L0X_define_Error_group Error and Warning code returned by API
 *	The following DEFINE are used to identify the PAL ERROR
 *	@{
 */

typedef int8_t VL53L0X_Error;

#define VL53L0X_ERROR_NONE			   ((VL53L0X_Error)	0)
#define VL53L0X_ERROR_CALIBRATION_WARNING	   ((VL53L0X_Error) - 1)
	/*!< Warning invalid calibration data may be in used
	 *	\a	VL53L0X_InitData()
	 *	\a VL53L0X_GetOffsetCalibrationData
	 *	\a VL53L0X_SetOffsetCalibrationData
	 */
#define VL53L0X_ERROR_MIN_CLIPPED		   ((VL53L0X_Error) - 2)
	/*!< Warning parameter passed was clipped to min before to be applied */
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

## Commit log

2025-12-20 Air-Sus Revision 1 (#1)
    * initial hardware
    * init
    * Air-Sus board added, breakout board started
    * filepath fixed
    * ir breakout board prototype finished
    * Temperature board schematic partially complete without testpoints.
    * finished schematic for all
    * small changes
    * added op-amp, finished footprints, new connector, fuse, ldo
    * added configurable options for board type/connector, cubemx ioc, nanofit for ir rideheight, added part numbers, etc.
    * air-sus layout check
    e Please enter the commit message for your change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
    [Air-Sus.kicad_pcb, Air-Sus.kicad_sch, LEDs.kicad_sch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]
2026-02-03 Rev B Review (#2)
    * schematic changes: ldo switched out of qfn, op amp footprint fixed, resistor array changed. need add correct stm changes
    * finished sch + removed LDO
    * removed LDO, added correct cube.
    * op-amp changes
    * layout finished, need to add some more silkscreen + ready for review!
    * finished layout + silkscreen, ready to review.
    * mac files removed
    * made changes from review council
    * added 3d models for 01x05 nanofits
    * added stepfiles for sus-rh
    * sus-rh production ready
    * remove .DS_Store files
    * fixed nanofit for linpot
    * added "validated silkscreen"
    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
    [Pitot.kicad_pcb, Pitot.kicad_sch, Pitot.step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]
2026-03-12 Pitot Board Rev B (#3)
    * added layout
    * ready to review
    * finished pitot board
    * pitot board ordered, routing+size finished for temperature board so pull??
    * finished tempboard silkscreen
    * resized temperature board
    * poo oo ee
    * ughhhhhhhhhhhhhhhhhhghghghhhhhhhhhhhhhhhhhhh
    * working i2c on RH board
    * cleanup?
    * small
    * added read me
    * fixed mistake
    * Fix image filename case in README.md
    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
    [Pitot-CuBottom.gbr, Pitot-CuTop.gbr, Pitot-EdgeCuts.gbr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]
2026-04-05 datapacking, working interrupts, and CAN Transmit working on linpots
    [Sus-RH.kicad_sch]
2026-04-05 finished linpot: - working recieve functionality from telem leader - automatic hz calculation - large fifo to hold data - timed interrupts - data packing via accumulator
2026-04-11 working cleaned suspension board
2026-04-12 working polling on i2c at 30hz. (rh)

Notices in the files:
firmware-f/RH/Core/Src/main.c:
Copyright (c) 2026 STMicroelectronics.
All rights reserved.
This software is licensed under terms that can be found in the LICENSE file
